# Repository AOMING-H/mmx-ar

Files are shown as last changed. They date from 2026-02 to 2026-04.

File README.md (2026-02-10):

# MMX AOMING Remix
## 简介
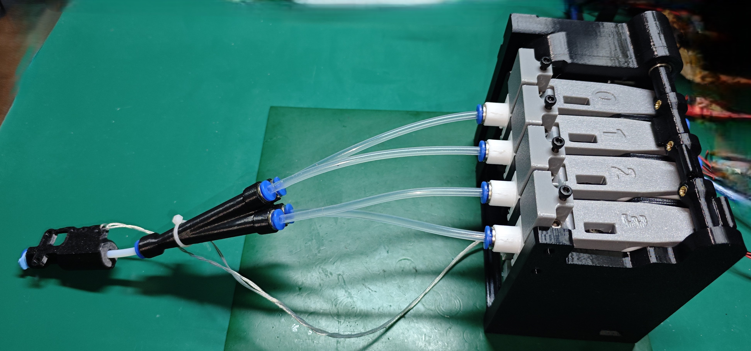
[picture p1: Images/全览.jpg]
全览

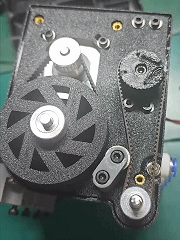
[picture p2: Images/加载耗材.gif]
加载耗材


原始工程
https://www.printables.com/model/1181017-mmx-multi-material-extruder-exclusive-final-releas

### 主要修改点
- 圆角调整为倒角, 便于打印和二次修改
- 调整凸轮轴固定方式, 现在轴承固定在中间的板上, 不用侧盖也能正常工作了
- 使用16T同步轮或20T同步轮代替凸轮轴打印的同步轮
- 增加弹簧下压机构, 可以调节下压力度, 且维护BMG齿轮不用再拆开整个机器了
- 修改舵机主动轮, 通过与注塑的舵机主动轮结合, 更不容易打滑, 且可以使用开口同步带替换闭口同步带
- 绘制了基于RP2040的专用主板 - https://oshwhub.com/aoming/3d-da-yin-mmx-duo-se-zhu-ban

### 打印注意事项
- 建议使用PETG进行打印
- 建议使用Voron结构件打印参数进行打印
    - 顶底5层, 壁厚4, 填充40%
- 请自行观察模型, 加上支撑

## 交流QQ群
1027251200

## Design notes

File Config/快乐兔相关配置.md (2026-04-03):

本文档仅针对Voron2.4以及SB头有效, 其它版本请自行进行调整

本文档不详细介绍如何进行多色调试, 仅提供对应配置文件, 详细多色调试请参考胖松鼠分享的文档以及对应视频

https://docs.qq.com/doc/DQndFeFp6RUZ0eHli

## printer.cfg文件引用
前两个为MMX多色需要的引用
后一个分别为 喷嘴清理所需要 的引用
```
[include mmu/base/*.cfg]
[include mmu/optional/client_macros.cfg]
[include wipe-nozzle.cfg]
```
保存后重启, 并确认归位操作正常

## mmu/base/mmu_macro_vars.cfg
以下为需要修改的配置, 请找到对应位置进行替换
```
variable_cutting_axis		    : "x"		; 切断耗材时, 工具头的运动方向
variable_pin_loc_xy             : 20, 290	; 切刀臂刚接触撞击块的坐标, 请自行调整
variable_pin_park_dist          : 5.0		; 切刀动作前加速的距离
variable_pin_loc_compressed_xy  : -4, 290	; 最后压缩状态的X坐标, 这里设置过头会丢步

variable_blade_pos              : 60.0		; 切割刀片刀喷嘴尖端的距离
variable_retract_length         : 30.0		; 切割之前回抽的距离

# 以下为换料过程中停车位置
variable_park_toolchange        : -999, -999, 1,  5, 2	; x,y,z-hop,z_hop_ramp,retract for "toolchange" operations (toolchange,load,unload)
variable_park_runout            : -999, -999, 1,  5, 2	; x,y,z-hop,z_hop_ramp,retract
variable_park_pause             : 60,   300,   5,  0, 2	; x,y,z-hop,z_hop_ramp,retract (park position when mmu error occurs)
variable_park_cancel            : -999, -999, 10, 0, 5	; x,y,z-hop,z_hop_ramp,retract
variable_park_complete          : 60,   300,   10, 0, 5	; x,y,z-hop,z_hop_ramp,retract

variable_pre_unload_position    : -999, -999, 0	; x,y,z-hop position before unloading starts
variable_post_form_tip_position : -999, -999, 0	; x,y,z-hop position after form/cut tip on unload
variable_pre_load_position      : 60,   300, 0	; x,y,z-hop position before loading starts, 
variable_restore_xy_pos         : "next"	; 控制工具头（x,y）在执行停车动作后的返回位置 

variable_user_post_form_tip_extension       : 'MOVE_TO_WIPE_NOZZLE_POS'	; 尖端成型之后执行的宏
variable_user_post_load_extension           : 'WIPE_NOZZLE'	            ; 加载料之后执行的宏
```

## mmu/base/mmu_hardware.cfg
stepper_mmu_gear 和 stepper_mmu_selector 可适当调整挤出机电流和其他参数
以下为需要修改的配置, 请找到对应位置进行替换
```
extruder_switch_pin: PBXX                   # 挤出机传感器上, 请自行更换对应引脚
toolhead_switch_pin: PBXX                   # 挤出机传感器下, 请自行更换对应引脚
sync_feedback_tension_pin: ^mmu:MMU_BELAY   # 在灯丝张力下触发的开关传感器
sync_feedback_compression_pin:              # 在灯丝压缩下触发的开关传感器

# 以下为LED配置, 请根据实际情况进行调整
[neopixel mmu_leds]
pin: mmu:MMU_NEOPIXEL
chain_count: 4			# 门的数量 x1 or x2 + 1 (如果你有状态LED)
color_order: GRB		# 设置neopixel灯珠的规格顺序

[mmu_leds unit0]
led_strip: neopixel:mmu_leds (4-1)
exit_range: 
entry_range: 
#status_index: 
frame_rate: 24
```
若使用的是4988, 请注释[tmc2209 stepper_mmu_gear]相关配置, 并将microsteps调整为16
LED动态灯效暂时没有办法通过配置关闭, 建议写个开机延时宏进行关闭

## mmu/base/mmu_parameters.cfg
以下为需要修改的配置, 请找到对应位置进行替换
```
gear_max_velocity: 100			# 耗材加载速度上限, 请根据个人情况修改
gear_max_accel: 500			    # 耗材加载加速度上限, 请根据个人情况修改
selector_max_velocity: 200		# 选料电机速度上限, 请根据个人情况修改
selector_max_accel: 1200		# 选料电机加速度上限, 请根据个人情况修改

gear_from_buffer_speed: 80		# 从缓存区加载耗材的速度, 请根据个人情况修改
gear_from_buffer_accel: 100		# 从缓存区加载耗材的加速度, 请根据个人情况修改
gear_from_spool_speed: 80		# 从料盘加载耗材的速度, 请根据个人情况修改
gear_from_spool_accel: 100		# 从料盘加载耗材的加速度, 请根据个人情况修改

toolhead_extruder_to_nozzle: 85		# 挤出机齿轮啮合位置到喷嘴尖端的距离
toolhead_sensor_to_nozzle: 75		    # 工具头传感器（挤出机下方）到喷嘴尖端的距离
toolhead_entry_to_extruder: 13		# 挤出机入口传感器到挤出机啮合位置的距离
toolhead_residual_filament: 22		    # 喷嘴中耗材卸载后残留耗材长度(对于大流量热端，比如TZ2.0，此值比较大，大约23)
toolhead_ooze_reduction: 2		        # 修复最后可能的漏料问题，一般是一个很小的数，大于零表示减少加载量

extruder_homing_max: 120			    # 耗材慢速加载的最大距离
extruder_homing_endstop: extruder	    # 耗材加载到位检测方式, 这里直接指定使用挤出机上方传感器
extruder_homing_buffer: 25			    # 鲍登长度减掉这个距离, 然后慢速靠近微动
extruder_collision_homing_current: 30	# 归位到挤出机时使用的步进电机电流（10%-100%）
extruder_force_homing: 1                # 强制开始挤出机归位, 避免进料时出现剧烈碰撞

force_form_tip_standalone: 1		    # 使用快乐兔全权负责尖端处理
form_tip_macro: _MMU_CUT_TIP            # 调用快乐兔切刀的宏

sync_to_extruder: 1			# 在打印过程中使兔子的齿轮送料电机和挤出机电机同步，设置为1
sync_gear_current: 70		# 百分比% 在同步挤出时，齿轮送料电机的电流为正常状态的百分比(10%-100%)
sync_form_tip: 1			# 尖端处理的时候是否采用同步
sync_purge: 1				# Synchronize during standalone purging (last part of load)

sync_feedback_enable: 1			# 0 = 关闭 (即使安装了传感器), 1 = 开启(仅在打印过程中)
sync_multiplier_high: 1.15		# 应用于齿轮步进器“旋转_距离”的最大系数, 请根据个人情况修改
sync_multiplier_low: 0.85		# 应用于齿轮步进器“旋转_距离”的最小系数, 请根据个人情况修改

retry_tool_change_on_error: 1	# 开启错误自动恢复

gate_preload_homing_max: 250		# 耗材就位的拉取距离
```

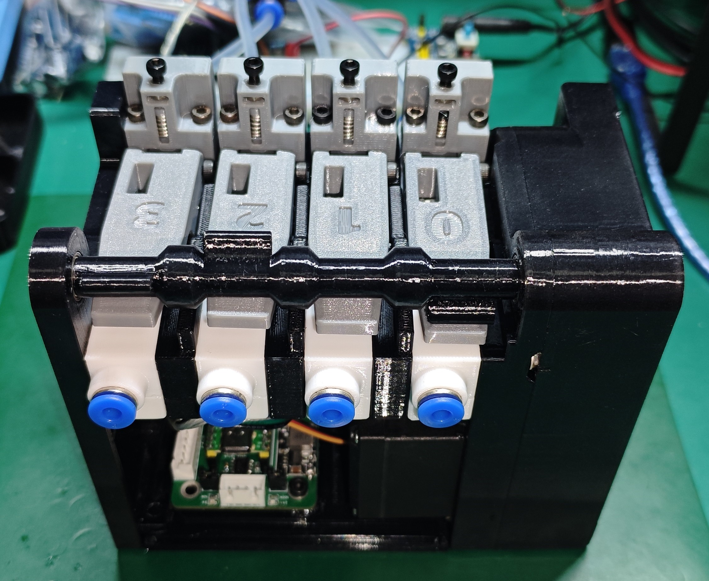
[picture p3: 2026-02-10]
Images/后面.jpg

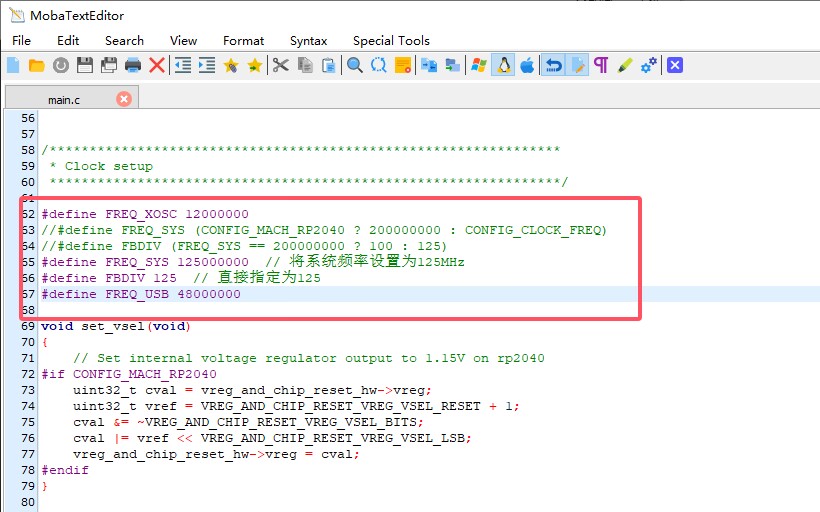
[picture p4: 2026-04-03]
Images/RP2040降频.jpg

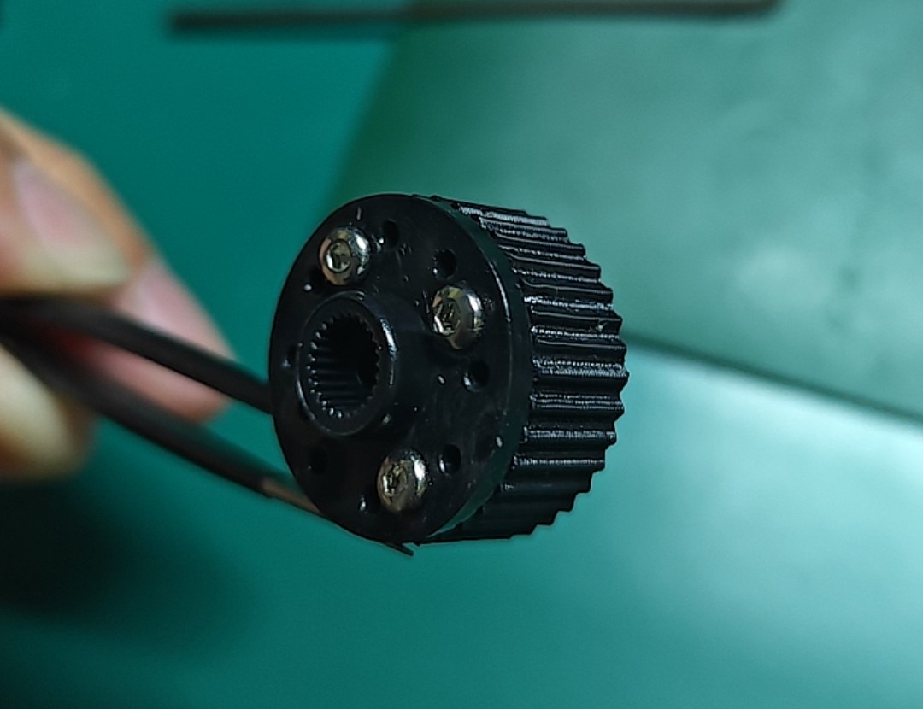
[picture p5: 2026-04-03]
Images/舵机同步轮安装.jpg

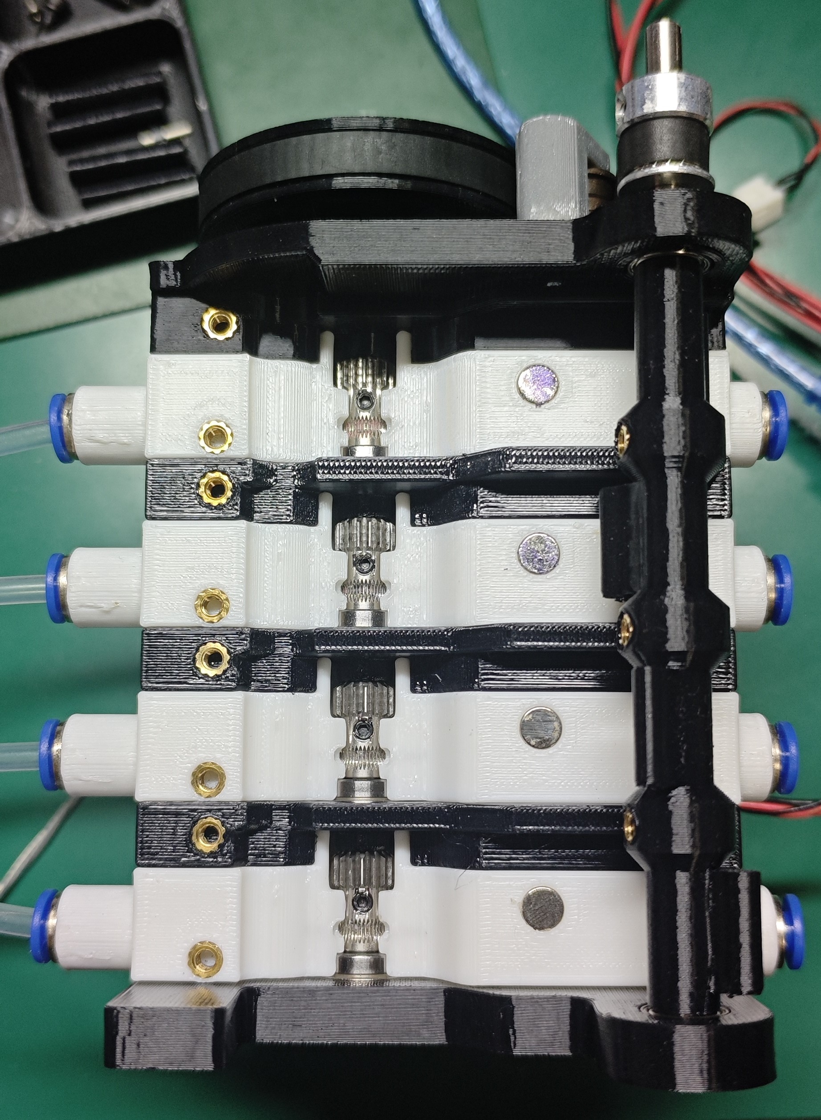
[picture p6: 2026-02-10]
Images/顶面.jpg

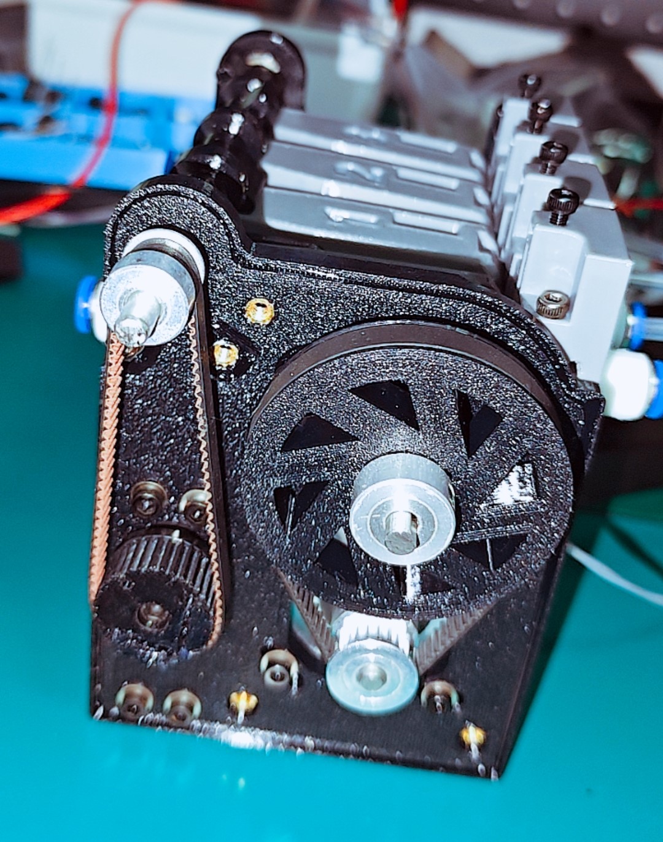
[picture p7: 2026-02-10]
Images/侧面.jpg

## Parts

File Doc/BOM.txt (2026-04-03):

https://docs.qq.com/sheet/DVmNwSU5VU2hyd2tE?no_promotion=1&is_blank_or_template=blank&tab=qg30tf

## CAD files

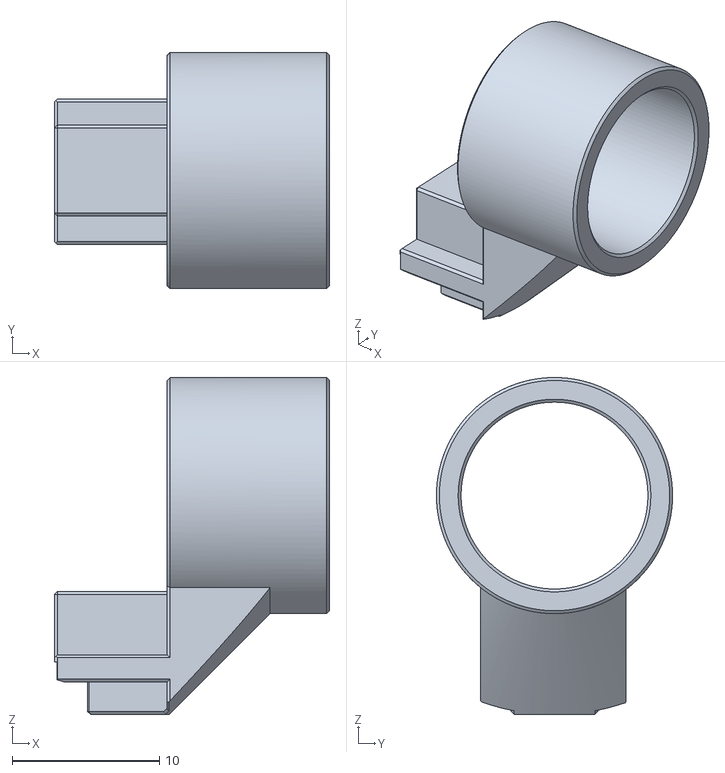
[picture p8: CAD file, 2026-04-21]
STL/通道门导光罩-x4.stl
18.7 x 16.1 x 22.9

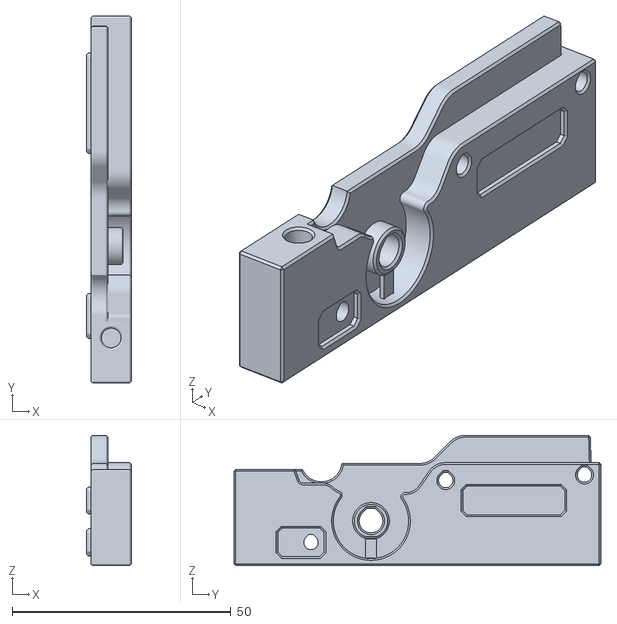
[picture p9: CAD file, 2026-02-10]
STL/通道门隔板-x3.stl
10.2 x 83.9 x 29.8

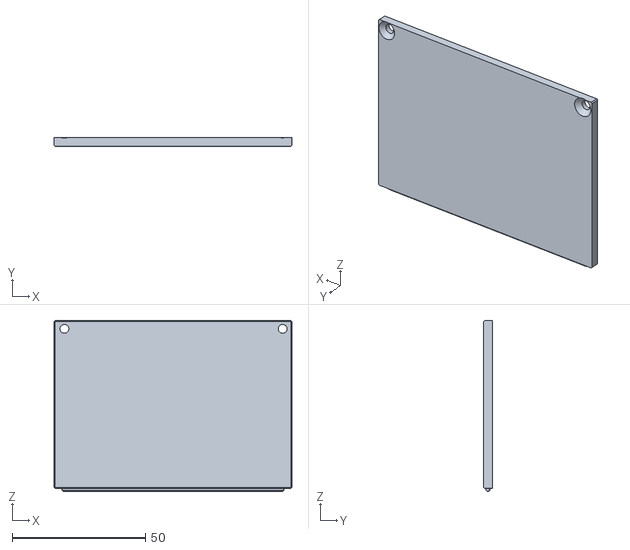
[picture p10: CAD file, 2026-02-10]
STL/侧板-后.stl
89.2 x 3.34 x 64.1

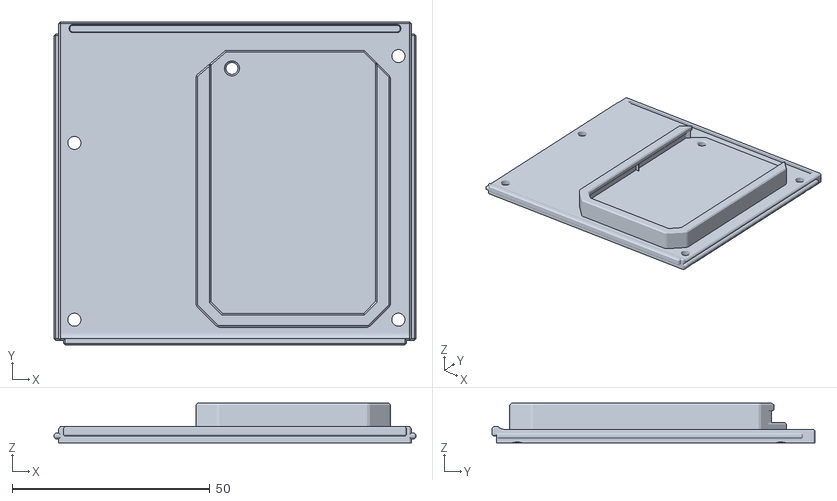
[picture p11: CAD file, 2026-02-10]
STL/底板.stl
91.6 x 81.7 x 10.00

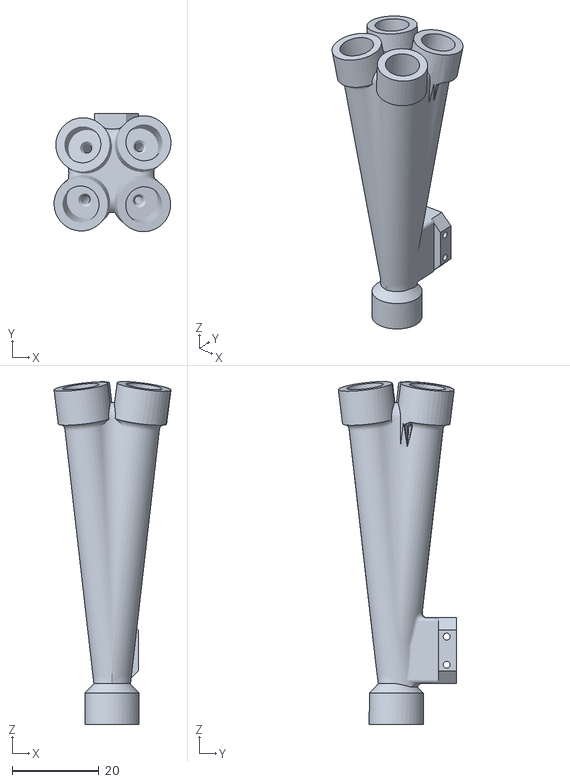
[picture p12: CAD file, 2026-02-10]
STL/四进一出带微动-适配非标鲍登头.STL
27.1 x 27.4 x 79.3

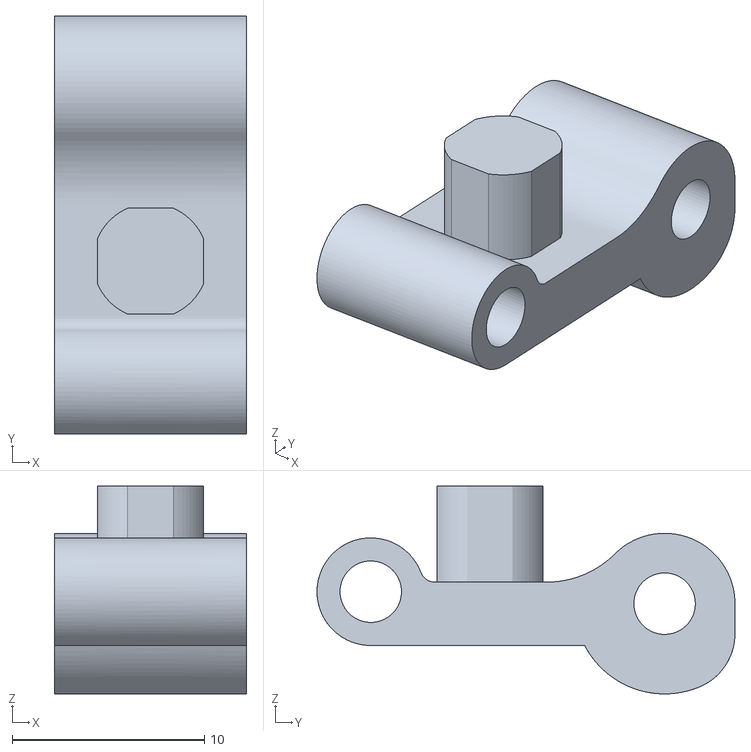
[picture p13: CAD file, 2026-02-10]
STL/连杆-x4.stl
10.0 x 21.8 x 10.8

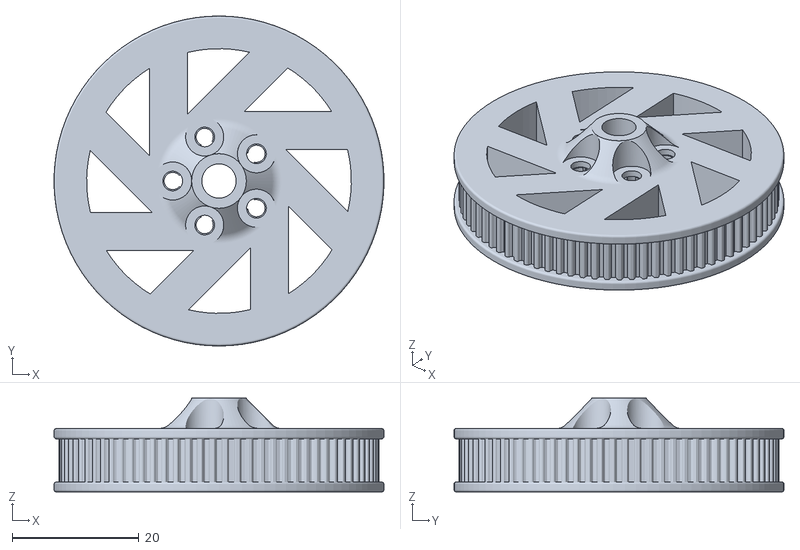
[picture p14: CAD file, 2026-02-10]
STL/80T齿轮.stl
52.0 x 52.0 x 14.8

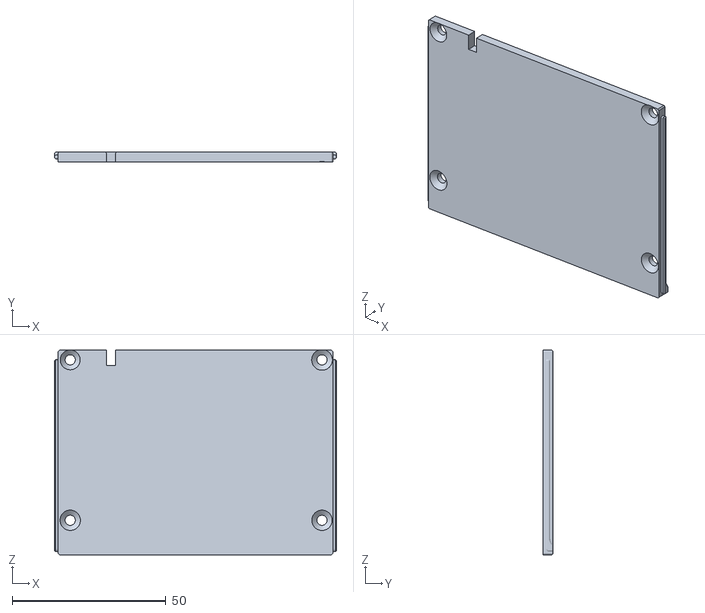
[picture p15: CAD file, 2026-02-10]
STL/侧板-前.stl
91.6 x 3.31 x 66.5

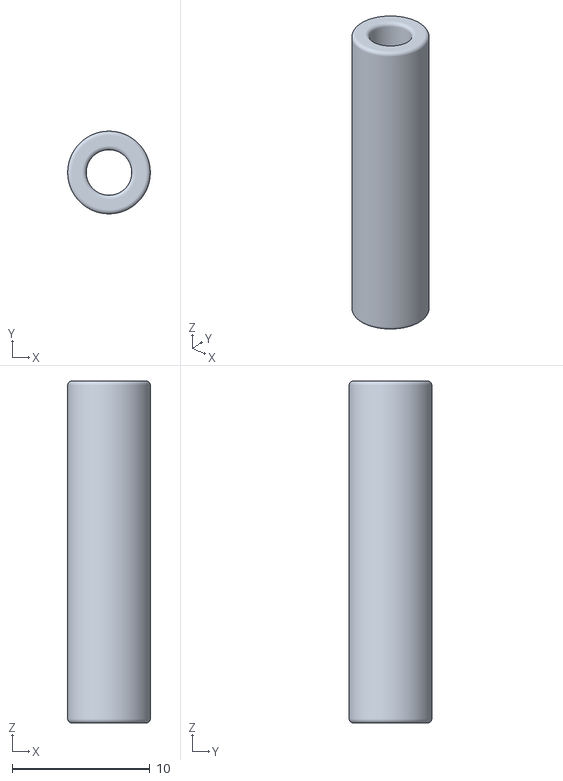
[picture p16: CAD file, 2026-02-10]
STL/侧板-右-支柱-x4.stl
6.00 x 6.00 x 24.8

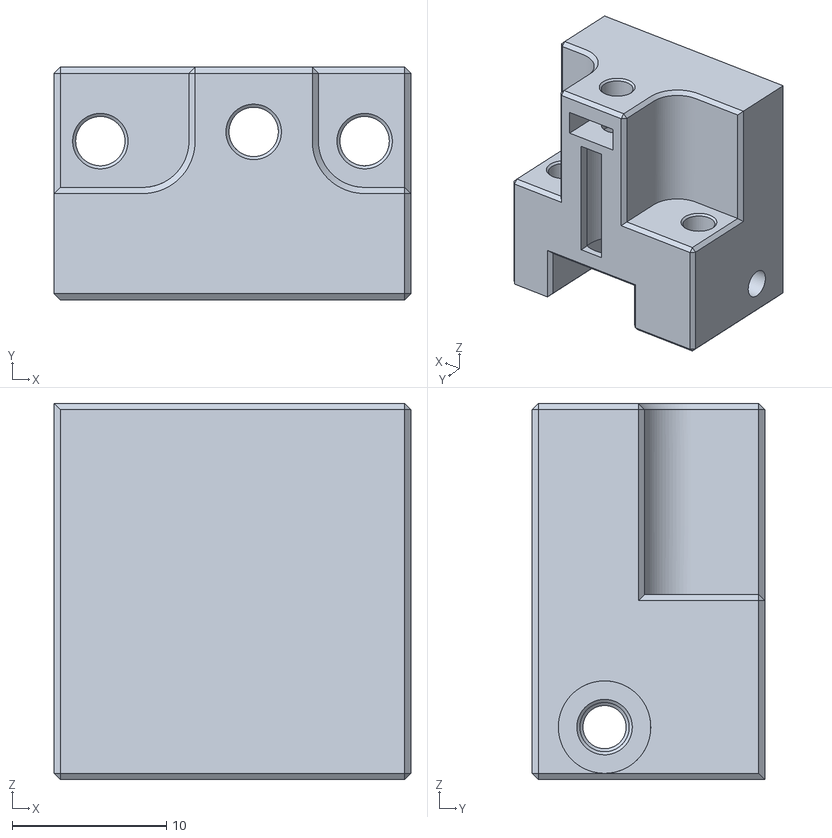
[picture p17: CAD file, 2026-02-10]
STL/连杆固定-x4.stl
23.2 x 15.1 x 24.4

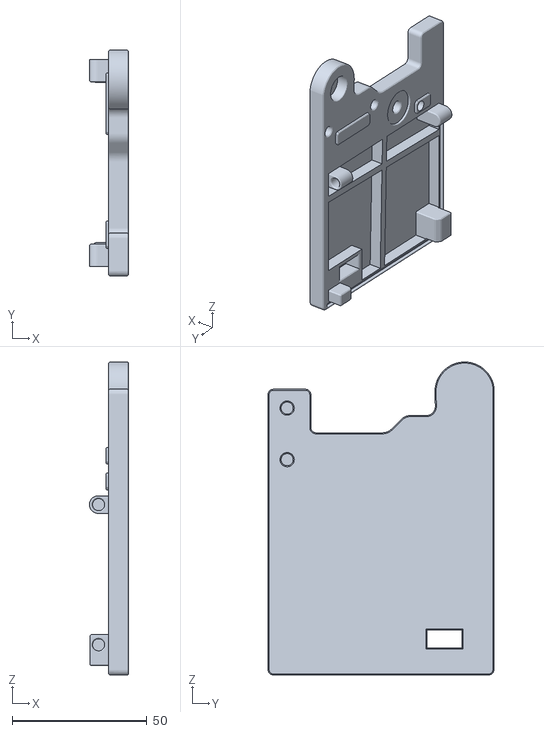
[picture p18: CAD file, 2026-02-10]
STL/侧板-左.stl
14.6 x 84.0 x 116.3

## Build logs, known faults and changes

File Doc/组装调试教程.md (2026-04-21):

# 原版MMX视频教程
https://www.bilibili.com/video/BV1FgqUBhEvV

# MMX-AR补充说明
1. 如果是拆下的鲍登头, 会比标准鲍登头大一圈, 要打印非标鲍登头版本的打印件
2. 996R的圆型舵机盘需要保留, 通过3个m2自攻螺丝与打印件结合, 更不容易打滑, 若皮带容易脱出, 确定长度之后可以上胶水
3. 凸轮轴固定使用M3机米螺丝, 通常4MM长够用, 若D轴较深请自己适当再加长, 若没有机米螺丝, 可以直接胶水或者其他方式固定
4. 舵机下压角度请确保完全垂直, 否则可能会打滑
5. 如果钢珠和微动中间有间隙, 可以垫合适厚度的胶带处理

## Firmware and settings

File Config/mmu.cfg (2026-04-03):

########################################################################################################################
# Happy Hare MMU Software
#
# EDIT THIS FILE BASED ON YOUR SETUP
#
# Copyright (C) 2022-2025  moggieuk#6538 (discord)
#                          moggieuk@hotmail.com
# This file may be distributed under the terms of the GNU GPLv3 license.
#
# Goal: Happy Hare MMU hardware pin config
#
# (\_/)
# ( *,*)
# (")_(") Happy Hare Ready
#
#
# This contains aliases for pins for MCU type unknown
#
[mcu mmu]
# serial: /dev/serial/by-id/XXX	# Change to `canbus_uuid: 1234567890` for CANbus setups
canbus_uuid: xxxxxx

# PIN ALIASES FOR MMU MCU BOARD ----------------------------------------------------------------------------------------
# ██████╗ ██╗███╗   ██╗     █████╗ ██╗     ██╗ █████╗ ███████╗
# ██╔══██╗██║████╗  ██║    ██╔══██╗██║     ██║██╔══██╗██╔════╝
# ██████╔╝██║██╔██╗ ██║    ███████║██║     ██║███████║███████╗
# ██╔═══╝ ██║██║╚██╗██║    ██╔══██║██║     ██║██╔══██║╚════██║
# ██║     ██║██║ ╚████║    ██║  ██║███████╗██║██║  ██║███████║
# ╚═╝     ╚═╝╚═╝  ╚═══╝    ╚═╝  ╚═╝╚══════╝╚═╝╚═╝  ╚═╝╚══════╝
# Section to create alias for pins used by MMU for easier integration into Klippain and RatOS. The names match those
# referenced in the mmu_hardware.cfg file. If you get into difficulty you can also comment out this aliases definition
# completely and configure the pin names directly into mmu_hardware.cfg. However, use of aliases is encouraged.

# Note: that aliases are not created for TOOLHEAD_SENSOR, EXTRUDER_SENSOR or SYNC_FEEDBACK_SENSORS because those are
# most likely on the printer's main mcu. These should be set directly in mmu_hardware.cfg
#
[board_pins mmu]
mcu: mmu # Assumes using an external / extra mcu dedicated to MMU
aliases:
    MMU_GEAR_UART=gpio14,
    MMU_GEAR_STEP=gpio12,
    MMU_GEAR_DIR=gpio13,
    MMU_GEAR_ENABLE=gpio11,
    MMU_GEAR_DIAG=,

    MMU_GEAR_UART_1={gear_1_uart_pin},
    MMU_GEAR_STEP_1={gear_1_step_pin},
    MMU_GEAR_DIR_1={gear_1_dir_pin},
    MMU_GEAR_ENABLE_1={gear_1_enable_pin},
    MMU_GEAR_DIAG_1={gear_1_diag_pin},

    MMU_GEAR_UART_2={gear_2_uart_pin},
    MMU_GEAR_STEP_2={gear_2_step_pin},
    MMU_GEAR_DIR_2={gear_2_dir_pin},
    MMU_GEAR_ENABLE_2={gear_2_enable_pin},
    MMU_GEAR_DIAG_2={gear_2_diag_pin},

    MMU_GEAR_UART_3={gear_3_uart_pin},
    MMU_GEAR_STEP_3={gear_3_step_pin},
    MMU_GEAR_DIR_3={gear_3_dir_pin},
    MMU_GEAR_ENABLE_3={gear_3_enable_pin},
    MMU_GEAR_DIAG_3={gear_3_diag_pin},

    MMU_SEL_UART=,
    MMU_SEL_STEP=,
    MMU_SEL_DIR=,
    MMU_SEL_ENABLE=,
    MMU_SEL_DIAG=,
    MMU_SEL_ENDSTOP=,
    MMU_SEL_SERVO=gpio29,

    MMU_ENCODER=,
    MMU_GATE_SENSOR=gpio27,
    MMU_NEOPIXEL=gpio26,

    MMU_PRE_GATE_0=gpio2,
    MMU_PRE_GATE_1=gpio3,
    MMU_PRE_GATE_2=gpio4,
    MMU_PRE_GATE_3=gpio5,
    MMU_PRE_GATE_4=,
    MMU_PRE_GATE_5=,
    MMU_PRE_GATE_6=,
    MMU_PRE_GATE_7=,
    MMU_PRE_GATE_8=,
    MMU_PRE_GATE_9=,
    MMU_PRE_GATE_10=,
    MMU_PRE_GATE_11=,

    MMU_POST_GEAR_0=,
    MMU_POST_GEAR_1=,
    MMU_POST_GEAR_2=,
    MMU_POST_GEAR_3=,
    MMU_POST_GEAR_4=,
    MMU_POST_GEAR_5=,
    MMU_POST_GEAR_6=,
    MMU_POST_GEAR_7=,
    MMU_POST_GEAR_8=,
    MMU_POST_GEAR_9=,
    MMU_POST_GEAR_10=,
    MMU_POST_GEAR_11=,

    MMU_ESPOOLER_RWD_0={espooler_rwd_0_pin},
    MMU_ESPOOLER_FWD_0={espooler_fwd_0_pin},
    MMU_ESPOOLER_EN_0={espooler_en_0_pin},
    MMU_ESPOOLER_TRIG_0=,
    MMU_ESPOOLER_RWD_1={espooler_rwd_1_pin},
    MMU_ESPOOLER_FWD_1={espooler_fwd_1_pin},
    MMU_ESPOOLER_EN_1={espooler_en_1_pin},
    MMU_ESPOOLER_TRIG_1=,
    MMU_ESPOOLER_RWD_2={espooler_rwd_2_pin},
    MMU_ESPOOLER_FWD_2={espooler_fwd_2_pin},
    MMU_ESPOOLER_EN_2={espooler_en_2_pin},
    MMU_ESPOOLER_TRIG_2=,
    MMU_ESPOOLER_RWD_3={espooler_rwd_3_pin},
    MMU_ESPOOLER_FWD_3={espooler_fwd_3_pin},
    MMU_ESPOOLER_EN_3={espooler_en_3_pin},
    MMU_ESPOOLER_TRIG_3=,

    MMU_BELAY=gpio10,

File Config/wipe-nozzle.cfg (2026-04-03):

[gcode_macro MOVE_TO_WIPE_NOZZLE_POS]
description: 移动到喷嘴清理位置
gcode:
  #M106 S0             #风扇关闭（防止挤出的料被吹走）
  G90
  G1 X20 F6000
  G1 Y300 F6000
  G1 Y310 F6000
  G1 X2 F6000


# 排废动作宏
[gcode_macro WIPE_NOZZLE]
description: 喷嘴清理
#请配置以下参数
variable_purge_x: 2                # 喷嘴排废料位置的x坐标
variable_purge_y: 310              # 喷嘴排废料位置的y坐标【整个擦嘴过程y坐标不变】
variable_retract_lengh: 2.0        # 回抽长度
variable_brush_loc_x: 15           # 喷嘴位于铁氟龙管上方的x坐标

#以下参数视情况修改
variable_brush_extra_dist: 10      # 在刷子左右擦拭两侧增加的行程
variable_wipe_qty: 4               # 擦拭次数
variable_wipe_spd: 100             # 擦拭速度

variable_purge_length: 80                     # 当未设置工具映射purge_volumes或参数PURGE_LENGTH时的默认冲刷长度。
variable_purge_length_minimum: 80             # 即使你没有更换工具，也绝对需要冲刷的最小长度。这是为了在打印前为喷嘴做准备
variable_purge_length_modifier: 0.85           # 切片软件传递的冲刷洗涤量通常有点浪费。可以在这里调整倍数以获得最佳值。
variable_max_iteration_length: 40             # 单次挤出的最大灯丝长度（mm）。

# 在计算完冲刷体积后额外添加的耗材长度。冲刷体积并不总是考虑到切刀，因此从红色到白色的交换可能足够长，但从白色到红色的交换可能太短。
#   你应该在什么时候改变这个值：
#   增加：当从深色到浅色的交换是好的，但从浅色到深色不是。
#   减少：当从浅色到深色的交换是好的，但从深色到浅色不是。不要忘记增加purge_length_modifier
variable_purge_length_addition: 20

gcode:
  {% if 'x' not in printer.toolhead.homed_axes or 'y' not in printer.toolhead.homed_axes %}
    G28  ; 如果X或Y没有归位，进行归位
  {% endif %}

  G90                         #所有轴使用绝对定位
  M83                         #挤出机使用相对定位

  ##------1.移动到挤出点
  G1 X{purge_x} Y{purge_y} F6000
  G92 E0              #重置挤出机
  M106 S0             #风扇关闭（防止挤出的料被吹走）

  {% set from_tool = printer.mmu.last_tool %}                 # 换料前的tool
  {% set to_tool = printer.mmu.tool %}                        # 换料后的tool
  {% set filament_cross_section = (1.75/2) ** 2 * 3.1415 %}   # 耗材截面积，1.75为耗材直径

  # 获取切片软件传递并经过快乐兔预处理的冲刷体积
  {% set pv = printer.mmu.slicer_tool_map.purge_volumes %}
  # 确定冲刷长度
  {% if params.PURGE_LENGTH %}      # 获取参数中的冲刷长度
    {action_respond_info("提供了冲刷长度参数PURGE_LENGTH")}
    {% set purge_len = params.PURGE_LENGTH|float %}
  {% elif from_tool == to_tool %}   # Tool没有改变的话不需要冲刷
    {action_respond_info("WIPE-NPZZLE: Tool没有变化 (T%s > T%s), " ~
      "priming" if purge_length_minimum else "skipping"  % (from_tool, to_tool))}
    {% set purge_len = 0 %}
  {% elif pv %}                     # 使用切片软件传递的冲刷体积map
    {% if printer.mmu.last_tool < 0 or printer.mmu.tool < 0 %}
      {action_respond_info("WIPE-NPZZLE: 不知道当前是哪一个 tool(s). 寻找洗涤最大值")}
      {% set purge_vol = pv|map('max')|max %}
    {% else %}
      {% set purge_vol = pv[from_tool][to_tool]|float * purge_length_modifier %}
      {action_respond_info("WIPE-NPZZLE: 更换Tool T%s > T%s" % (from_tool, to_tool))}
    {% endif %}
    {% set purge_len = purge_vol / filament_cross_section + purge_length_addition %}
  {% else %}                       # 使用配置变量
    {action_respond_info("WIPE-NPZZLE: 没有 toolmap 或者 PURGE_LENGTH. 使用默认值")}
    {% set purge_len = purge_length|float %}
  {% endif %}

  {% set purge_len = [purge_len,purge_length_minimum]|max %}   # 应用冲刷最小值

  {action_respond_info("WIPE-NPZZLE: 此次共需要挤出 %.2fmm 的冲刷耗材" % (purge_len|float))}

  # 去掉一开始挤出的30mm长度的耗材
  {% set purge_len = purge_len - 30 %}       # 去掉前面已经挤出的量
  {% set purge_len = [purge_len,10]|max %}   # 此次最少再挤出10mm

  {% set iterations = (purge_len / max_iteration_length)|round(0, 'ceil')|int %}   # 计算循环次数

  ## ==================================== 循环挤出耗材开始[复刻拓竹P1逻辑]  ====================================
  {% for n in range(iterations) %}
    {% set purge_amount_left = purge_len - (max_iteration_length * n) %}
    {% set extrude_amount = [purge_amount_left,max_iteration_length]|min %}

    {% if extrude_amount > 23.7 %}
      {% if n == 0 %}
        G1 E23.7 F300     # 第一次的启动部分不需要脉动冲洗
        G1 E{(extrude_amount - 23.7) * 0.02} F50
        G1 E{(extrude_amount - 23.7) * 0.23} F300
        G1 E{(extrude_amount - 23.7) * 0.02} F50
        G1 E{(extrude_amount - 23.7) * 0.23} F300
        G1 E{(extrude_amount - 23.7) * 0.02} F50
        G1 E{(extrude_amount - 23.7) * 0.23} F300
        G1 E{(extrude_amount - 23.7) * 0.02} F50
        G1 E{(extrude_amount - 23.7) * 0.23} F300
        #初始之后开始冷却 【不建议开启或者开小风，因为Voron风向会导致废料不成团】
        # M106 S100
      {% else %}
        G1 E{extrude_amount * 0.18} F300
        G1 E{extrude_amount * 0.02} F50
        G1 E{extrude_amount * 0.18} F300
        G1 E{extrude_amount * 0.02} F50
        G1 E{extrude_amount * 0.18} F300
        G1 E{extrude_amount * 0.02} F50
        G1 E{extrude_amount * 0.18} F300
        G1 E{extrude_amount * 0.02} F50
        G1 E{extrude_amount * 0.18} F300
        G1 E{extrude_amount * 0.02} F50
      {% endif %}
    {% else %}
      G1 E{extrude_amount} F600
    {% endif %}
  {% endfor %}

  G1 E-{retract_lengh} F1800   # 断开

  G92 E0
  ## ==================================== 循环挤出耗材结束[复刻拓竹P1逻辑]  ====================================
  M106 S255           # 冷却
  G4 P4000            # 驻留 P<毫秒>

  #------5.擦拭喷嘴
  {% for wipes in range(1, (wipe_qty + 1)) %}
    G1 X{brush_loc_x - brush_extra_dist} F{wipe_spd * 60}
    G1 X{brush_loc_x + brush_extra_dist} F{wipe_spd * 60}
  {% endfor %}
  # G1 X{brush_loc_x - brush_extra_dist} F{wipe_spd * 60}
 ##------6.归位
  G92 E0
  M107                 #关闭风扇

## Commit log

2026-02-10 初始化项目
    [80T齿轮.stl, 侧板-前.stl, 侧板-右-支柱-x4.stl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]
2026-04-03 补充说明文档
    [mmu.cfg, wipe-nozzle.cfg]
2026-04-21 添加导光罩/调整张紧器
    [通道门导光罩-x4.stl]
